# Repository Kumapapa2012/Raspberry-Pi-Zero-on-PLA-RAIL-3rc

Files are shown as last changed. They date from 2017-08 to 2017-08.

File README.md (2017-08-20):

# ※注意: 使用 Raspbian について
こちらの内容は、Raspbian の最新イメージ(2017-08-16-raspbian-stretch-lite.img)では動作しません(uv4l がインストールできません)。
これまで Debian8 ベースであったものが、最新版から、Debian9 ベースに変更されたためです。
試す場合はお手数ですが、こちらから、7/15 バージョンもしくはそれ以前を入手して使用してください。

Lite 版
http://downloads.raspberrypi.org/raspbian_lite/images/

通常 版
http://downloads.raspberrypi.org/raspbian_lite/images/

# Raspberry-Pi-Zero W 搭載プラレールについて
去年、Raspberry-Pi Zero の発売と同時に[初代プラレール](https://github.com/Kumapapa2012/Raspberry-Pi-Zero-on-PLA-RAIL)を作成。
これは USB の　Web カメラ、Wifi Dongle などをつけるため、 USB ハブを接続していました。  

しかし今年、Raspberry-Pi Zero W を運よく入手でき、これをプラレールに搭載しました。  
Wifi-Dongle が不要になり、またRaspberry-pi Camera モジュールを使用することで、USB WebCam も不要になりました。  
さらに最近は Zero-LiPo という Lipo バッテリーをRaspberry Pi Zero で使用するためのパーツも販売されており、これも使用しました。  
その結果、かなりすっきりとした構造になりました。  
ここでは、作成方法と、動かすためのコードを公開します。  


# 材料
## プラレール S-61　E233系湘南色 (単二電池バージョン)
<http://www.takaratomy.co.jp/products/lineup/detail/plarail470663.html>  
単二電池バージョンのE233系です。  
最近のプラレールは単三電池バージョンが主流ですが、単二電池バージョンもまだ上記タカラトミーの公式サイトで販売しています。  
アマゾンなどでも購入可能と思われます。

## Raspberry Pi Zero W
<https://www.switch-science.com/catalog/3200/>  
技適の関係で、日本取り扱い店からの入手が必要ですが、2017/08 現在入手しづらい状況が続いています。

## Raspberry Pi Camera Module + Cable
<https://shop.pimoroni.com/products/raspberry-pi-camera-module-v2-1-with-mount>  
<https://shop.pimoroni.com/products/camera-cable-raspberry-pi-zero-edition>  
Raspberry Pi Zero に取り付けるカメラとケーブル。  
Zero のカメラコネクタは通常の Raspberry Pi とサイズが全く異なるため、専用ケーブルが必要です。  
最近、Zero 専用のカメラも出ましたので、こちらを使用するのもいいかもしれません。  
<https://shop.pimoroni.com/products/raspberry-pi-zero-camera-module>

## Zero Lipo
<https://www.switch-science.com/catalog/3216/>
Li-PoバッテリーをRaspberry Pi シリーズで使用できるようにする電源コンバーターです。  
なお、今回はバッテリーコネクタを切除し、カメラと干渉する部分を切断しています。
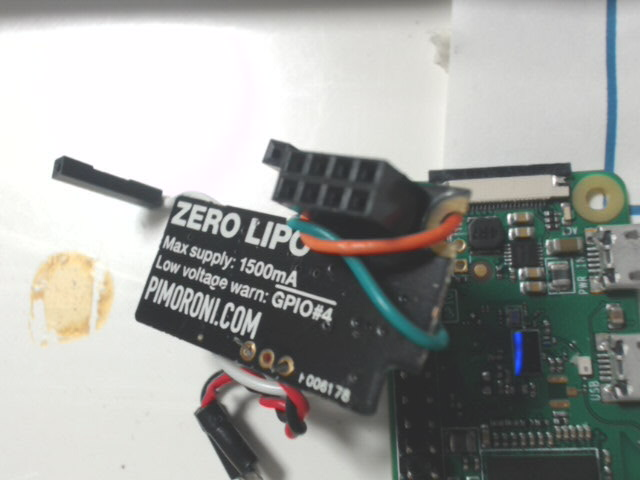
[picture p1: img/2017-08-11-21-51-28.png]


## Li-Po　バッテリー
<https://www.amazon.co.jp/gp/product/B01KC2JVB4/ref=oh_aui_detailpage_o04_s00?ie=UTF8&psc=1>  
Amazon で購入した、5個パック+充電器のセット。かなりコスパが良い。

## 電子部品
秋月電子さんや千石電商さんで購入。また、抵抗などは自宅にある適当なものを使用しています。  
以下の表にまとめます。

|種別|名称|備考|
|:-|:-|:-|
|モーターコントローラー|TA7291P|PWM によるモーター制御を行う|
|抵抗|R1|10kΩ - TA7291P の Vref-Vs間で、回路保護のため。|
|抵抗|R2|3.0Ω - Vs への入力電流の制限用|
|抵抗|R3|１kΩ - ヘッドランプ LED 用|
|LED|LED1,LED2|白色 LED ヘッドランプ用。|
|電解コンデンサ|C1|10V2200μF - 電圧降下の抑制用パスコン|
|コネクタ・ケーブル類|-|手持ちのものを使用|

## その他部品
バランス調整のため板おもりも使用しました。  
<https://www.amazon.co.jp/%E7%AC%AC%E4%B8%80%E7%B2%BE%E5%B7%A5-22170-%E6%9D%BF%E3%82%AA%E3%83%A2%E3%83%AA4m%E5%B7%BB%E3%82%AD-0-25mm/dp/B000AR6W00>

# 構造
モーター部とバッテリー部の2両で構成されています。
目測と手合わせだけで位置を決め、カッターやルーターでガリガリ切削して作っていますので図面等は存在しません。
このため、すべて写真で説明します。
※なお、以降の写真ではヘッドライトの LED が 1 つしかありません。これは先日結線が切れてしまい、外したためです。しかし以下の説明は、LED を2つ使うものとして記述します。

## 1 両目
Raspberry Pi Zero W とカメラ、モータードライバを搭載しています。カメラ画像は Motion JPEG ストリーミングしています。モータードライバでモーターの回転を制御します。  
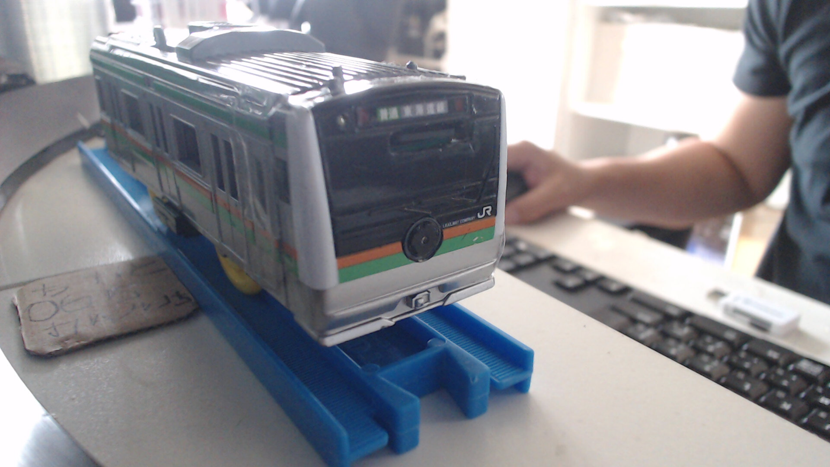
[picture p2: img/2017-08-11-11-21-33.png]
  
シャーシとの分離。  
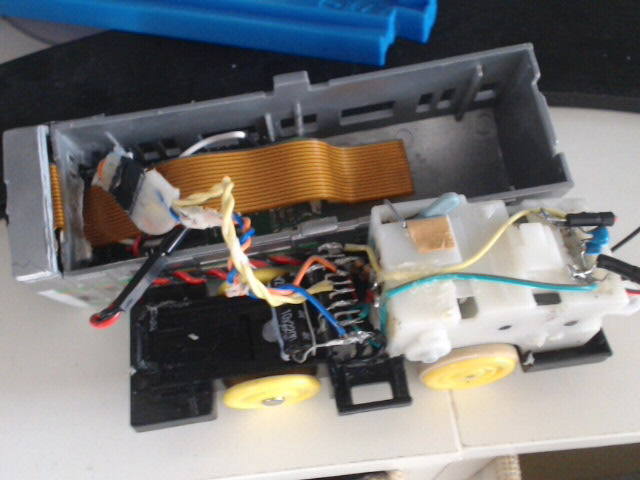
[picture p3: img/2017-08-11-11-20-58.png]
  
ケーブルを外したところ。  
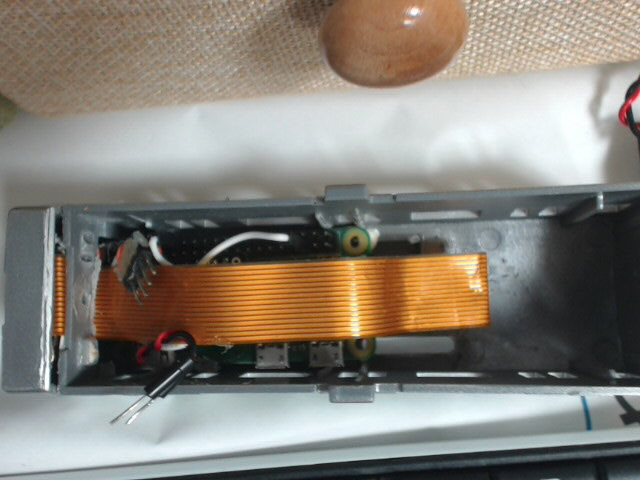
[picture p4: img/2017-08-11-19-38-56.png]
  
カメラケーブルを外したところ。  
中心の右下横のスイッチ穴に干渉しないよう、 Raspberry Pi Zero をはめています。こうしないと、ギヤボックスとRaspberry Pi Zero が干渉し、ボディがシャーシに嵌まりません。  
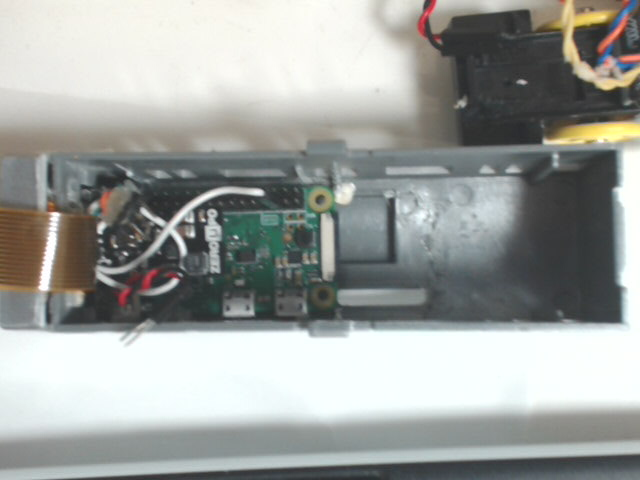
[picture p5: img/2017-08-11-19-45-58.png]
  
SD カードの突起により、スイッチ穴との干渉が発生したため、穴を開けて対処しています。  
結果的に、すぐに SD カードを取り出せるようになっています。  
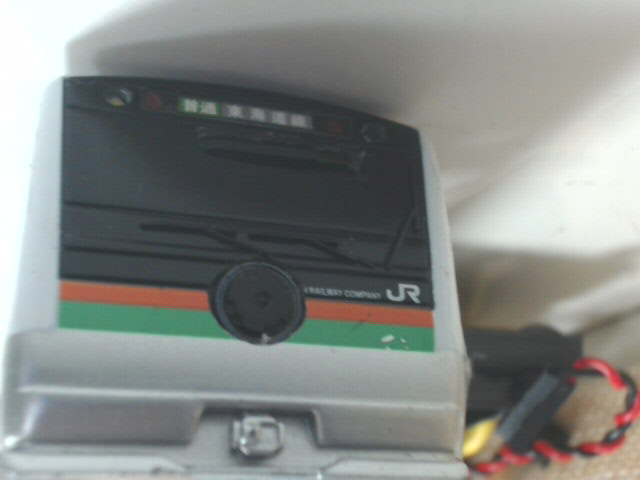
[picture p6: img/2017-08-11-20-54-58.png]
  
カメラの格納。運転席部分にすっぽりと収まります。  
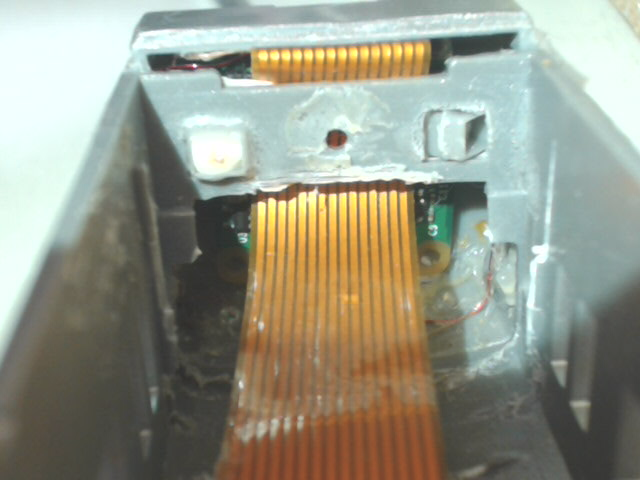
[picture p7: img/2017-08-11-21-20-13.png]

上から見たところ。ケーブルを下部にすることで、ケーブルが Raspberry Pi Zero と干渉するのを避けています。  
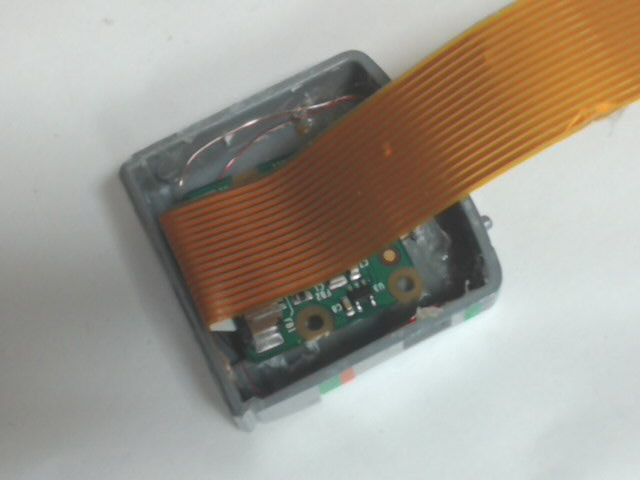
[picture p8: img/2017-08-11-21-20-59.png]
  
レンズの穴の位置も、やはり手合わせで決めています。  
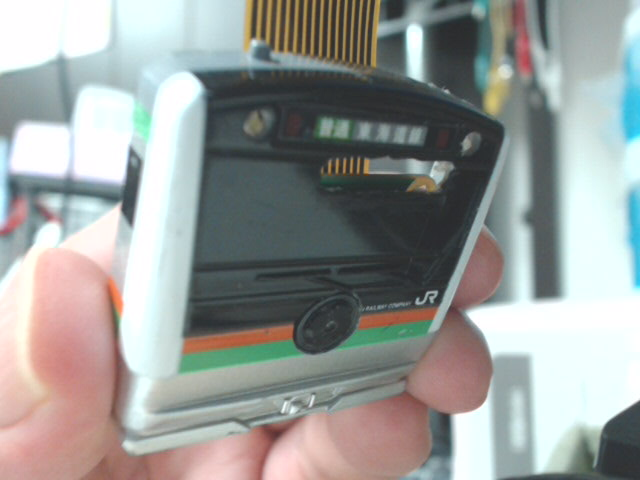
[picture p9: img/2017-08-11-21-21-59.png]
  
ボディ前方を大幅に切削したため運転席部分は保持できず、テープで止めています。  
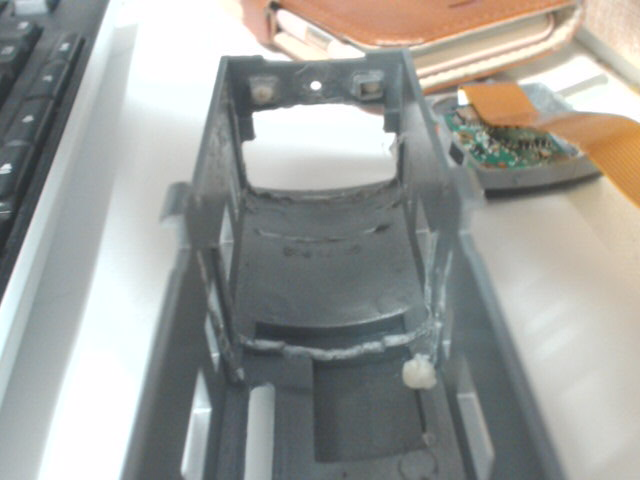
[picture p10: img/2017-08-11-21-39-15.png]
  
シャーシです。ハンダ付けが非常に雑で恥ずかしいのですが、一応問題なく機能しています。  
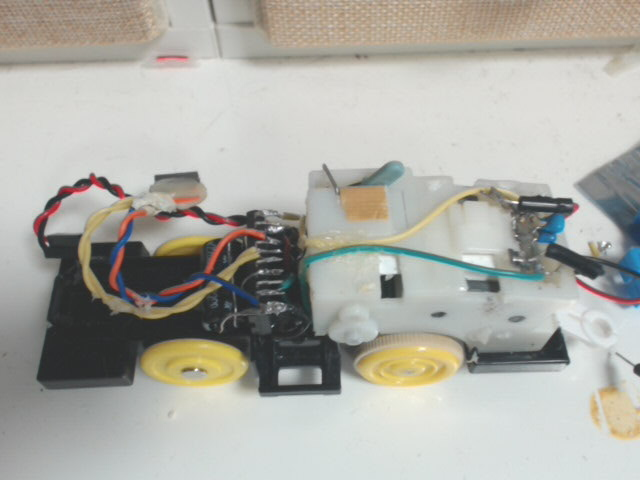
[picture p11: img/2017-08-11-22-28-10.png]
  
モータードライバとパスコンです。ハンダ付けが非常に汚く、見苦しいと思いますがご容赦ください。  
配線の詳細は別途記載する配線図にてご確認ください。  
なおパスコンは動作の安定化のためつけています。容量は適当です。  
これがないと、発進時にカーネルパニックを起こしがちです。  
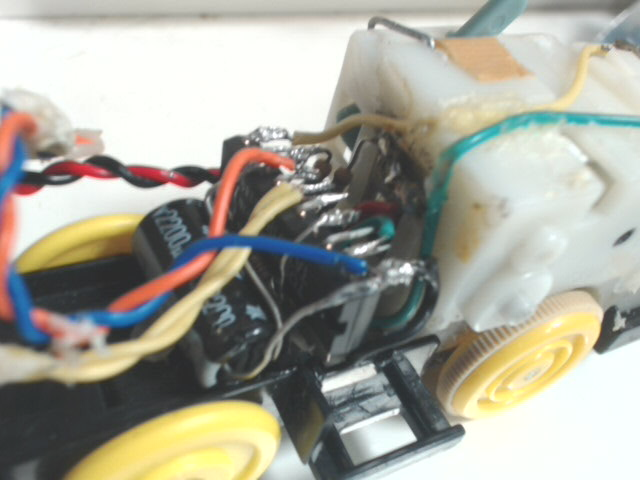
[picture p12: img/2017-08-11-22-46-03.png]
  
ギアボックスは 2 段階変速ですが、 1 段目のみ使用するようにストッパーを設けています。これはモータ負荷による起電力低下の緩和のためですが、そもそもブラウザでモーターの無段階変速を行いますので、ギアによる変速は無用です。  
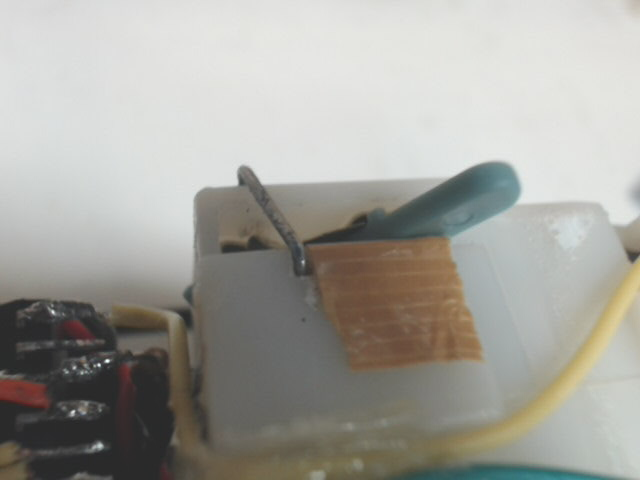
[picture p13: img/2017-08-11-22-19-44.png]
  
単二電池仕様のプラレールですので、電池がない状態では前輪が浮くことがあります。  
それを防止するため、前方下部におもりをつけています。板おもりを丸めて作成しています。
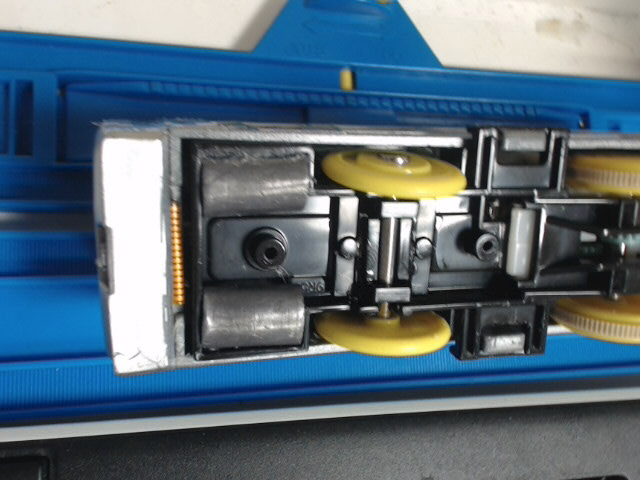
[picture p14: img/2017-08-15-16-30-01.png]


## 2 両目
Li-Po バッテリーを搭載しています。特に改造していません。 
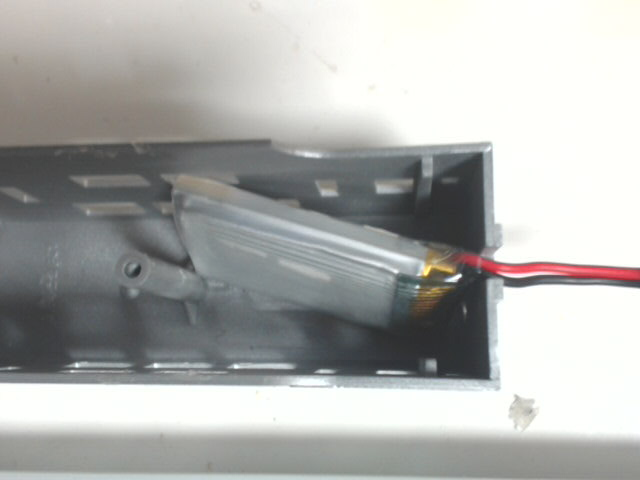
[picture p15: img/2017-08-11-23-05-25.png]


電池の充電は、車両ごと充電器に繋いで行います。
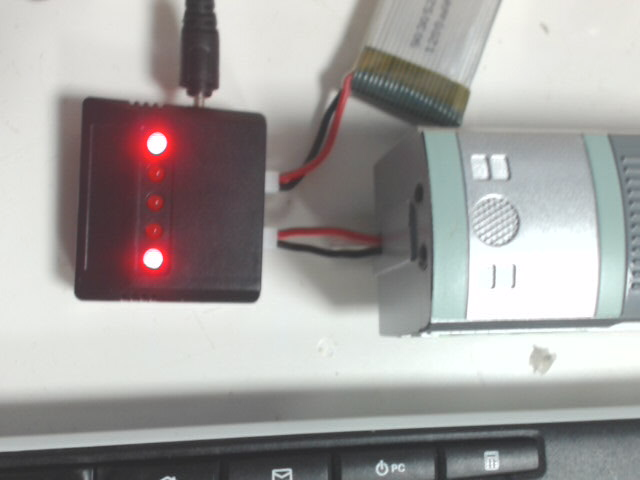
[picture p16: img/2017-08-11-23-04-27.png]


# ブレッドボード図/配線図
Fritzing で作成したブレッドボード図です。[Fritzing でも公開](http://fritzing.org/projects/raspberry-pi-zero-w-motor-control-with-zero-lipo-2)しています。   
左側ブレッドボードと Raspi の間の黒いチップは Zero LiPo です。  
なお図面では Raspberry Pi カメラモジュールは省略しています。  
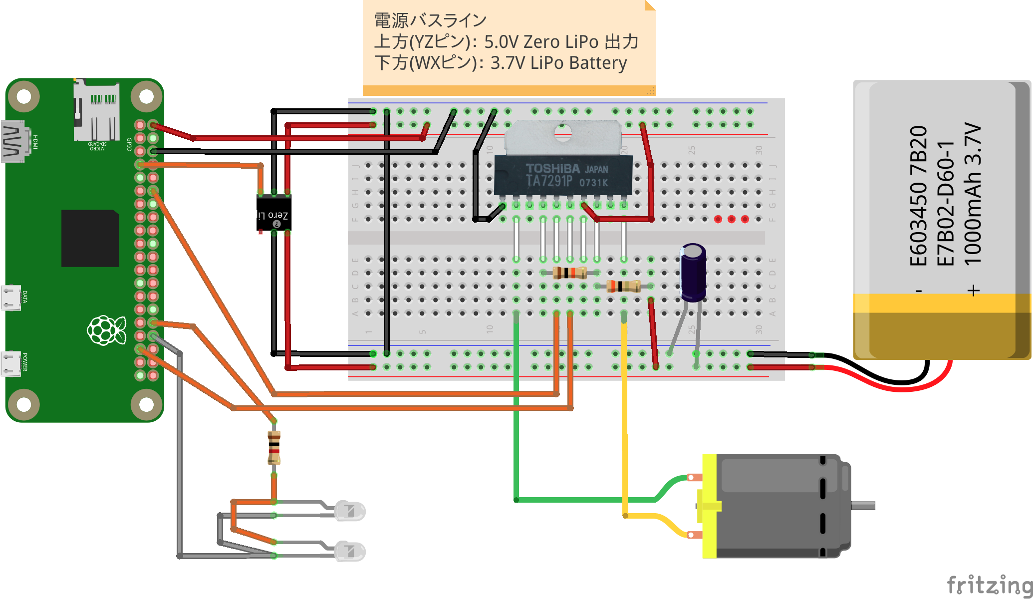
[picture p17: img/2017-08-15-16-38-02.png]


# ソフトウェア
プラレールは以下のような構成で動作します。
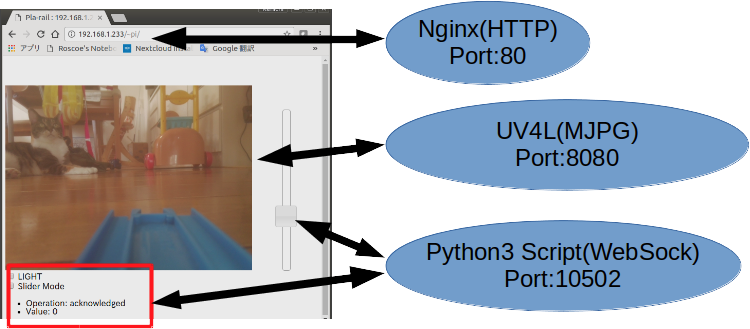
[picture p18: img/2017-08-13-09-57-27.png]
  
以下、セットアップ手順を説明します。  

## OS
SD カードにソフトウェアをインストールします。
OS は Raspbian 8 (Jessie) です。[公式サイト](https://www.raspberrypi.org/downloads/raspbian/)から入手してインストールしてください。  
OS のインストール後、"raspi-config" にて以下を有効化しておいてください。  
- Wifi 
- SSH 
- GPIO
- カメラ

また、Wifi経由の インターネットアクセス設定を行い、SSH で接続できることを確認しておいてください。  
これらの設定についてはここでは説明しません。

## Git からのファイル入手
本リポジトリにプラレール制御用ファイル群を公開しています。
SSH で Raspberry Pi Zero にログオンし、以下にて、Raspberry Pi Zero W にファイルを落としておきます。

$ cd ~  
$ sudo apt install git    
$ cd git  
$ git clone (本リポジトリのURL)  

## Nginx
ブラウザ等でプラレールをコントロールするページを表示するための Web サーバーになります。
### インストールと設定
apt でインストールします  

    $ sudo apt install nginx  

インストール後、``/etc/nginx/sites-available/default`` の ``"server {...}"``　セクションで、ユーザーフォルダの設定を行います。  
これにより、"http://hostname/~username/"で HTML コンテンツを公開できるようにします。  
以下を、``"server {...}"``　セクション内に追記します。

    location ~ ^/~(.+?)(/.*)?$ {  
        alias /home/$1/public_html$2;  
        index  index.html index.htm;  
        autoindex on;  
    }  

設定後、以下の作業を行い、ファイルを配置します。  

    $ cd ~  
    $ cp -R git/Raspberry-Pi-Zero-on-PLA-RAIL-3rd/public_html/ .

## UV4L
Motion JPEG による動画配信を行います。 "MJPEG Streamer" よりも新しく、取り扱いが簡単です。  
### インストールと設定
以下の手順でインストールします。  

    $ curl http://www.linux-projects.org/listing/uv4l_repo/lrkey.asc | sudo apt-key add -  
    $ sudo -s  
    # echo "deb http://www.linux-projects.org/listing/uv4l_repo/raspbian/ jessie main" >> /etc/apt/sources.list  
    # apt update  
    # apt install uv4l-webrtc uv4l-raspicam-extras  
    # exit  

インストール後、uv4l サービスを停止します。  

    $ sudo service uv4l_raspicam stop  

停止後、画像サイズを設定するため、"/etc/uv4l/uv4l-raspicam.conf" ファイルの以下のオプションを書き換えます。  

    width = 480  
    height = 360  
    framerate = 15  

書き換え後、uv4l サービスを起動します。  

    $ sudo service uv4l_raspicam start

## Python3 Script
モーター及び LED の制御を行います。  
WebSocket サーバーとして動作し、ブラウザ上で双方向リアルタイム制御を行うための機能を実装しています。  
### インストールと設定
以下インストールします。

    $ sudo apt install python3 python3-rpi.gpio python-pip python3-pip  
    $ pip3 install asyncio websockets

インストール後、以下のようにファイルを配置します。  

    $ cd ~  
    $ sudo cp -R git/Raspberry-Pi-Zero-on-PLA-RAIL-3rd/bin/ /opt/pla-rail/

起動時にスクリプトが動作するように、以下の作業を行います。

    $ sudo -s
    # crontab -e
    **** 表示された内容の最後に以下を記し保存します。****  

    # Run wsock_svr.py at boot time
    @reboot python3 /opt/pla-rail/wsock_svr.py &  

    **** 保存後 Root 状態から出ます。****  
    # exit  
    $

# テスト
一度 OS を再起動し、しばらくしてからブラウザで "http://(IP Address)/~pi/" を開きます。
以下のように画面が開き、カメラの映像が見えれば、起動しています。  
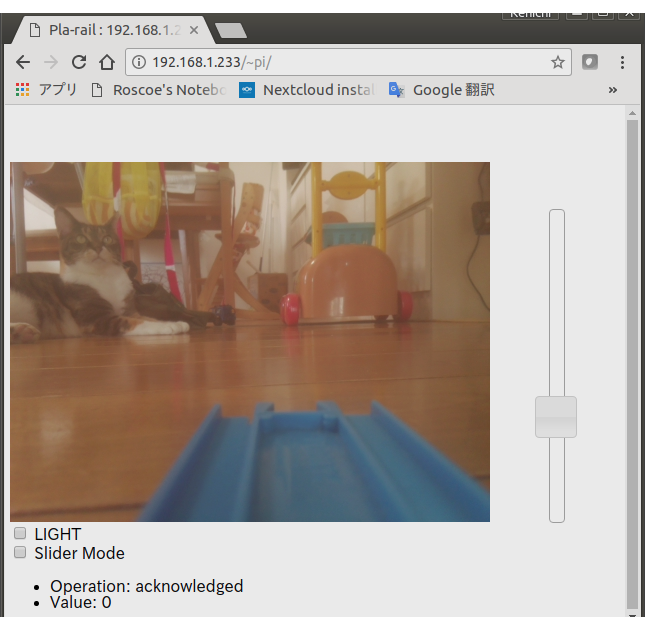
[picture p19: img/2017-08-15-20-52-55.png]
   
なお、"Operation..." が表示されていない場合、Python3 の WebSocket サーバーが動作していません。  
スクリプトが起動失敗していないか確認してください。

# 注意点
今回の場合、Zero Ripo バッテリー容量低下シグナル(GPIO4)の読み取りと通知は使用できません。これは、 1 つの LiPo バッテリーをモーター駆動と Raspberry Pi Zero 駆動の両方に使用しているためです。  
Zero Ripo バッテリー容量低下シグナルは起電力が 3.4V 程度になった場合に稼働しますが、今回の回路では、 3.8V 程度ですでに電力不足となり、モーター駆動の瞬間にダウンするようになります。このため、バッテリーの起電力が 3.4V 程度になるまで使用することはありません。

# 参考とさせていただいた文書
[Raspberry Pi 3 の標準カメラで撮影した動画をブラウザに配信する方法まとめ](http://qiita.com/okaxaki/items/72226a0b0f5fab0ec9e9#%E9%85%8D%E4%BF%A1%E6%96%B9%E6%B3%952---uv4l-raspicam)  
[Pythonスクリプトをサービスで起動させる](http://qiita.com/okhiroyuki/items/d19e8b0c4599767955a8)

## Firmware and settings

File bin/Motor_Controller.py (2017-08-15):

#!/usr/bin/env python3
# -*- coding: utf-8 -*-

import RPi.GPIO as GPIO
import time


class Motor_Controller:
	def __init__(self):
		# 初期化、BCM18→PWM0、BCM19→PWM1
		pwm0_pin=18
		pwm1_pin=19

		GPIO.setmode(GPIO.BCM)
		GPIO.setup(pwm0_pin, GPIO.OUT) 
		GPIO.setup(pwm1_pin, GPIO.OUT)
		
		self.pwm0=GPIO.PWM(pwm0_pin, 50)
		self.pwm1=GPIO.PWM(pwm1_pin, 50)

		self.pwm0.start(0)
		self.pwm1.start(0)


	def motor_run(self, duty):
		if duty>100: duty=100
		elif duty<-100: duty=-100
		absduty = min(abs(duty),100)
		
		if duty>0:
			self.pwm0.ChangeDutyCycle(absduty)
			self.pwm1.ChangeDutyCycle(0)
		elif duty<0:
			duty = max(abs(duty),100)
			self.pwm0.ChangeDutyCycle(0)
			self.pwm1.ChangeDutyCycle(absduty)
		else: # duty==0
			self.pwm0.ChangeDutyCycle(0)
			self.pwm1.ChangeDutyCycle(0)

	def __del__(self):
		GPIO.cleanup()

if __name__ == "__main__":
	pass

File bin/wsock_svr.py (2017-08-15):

#!/usr/bin/python3
# -*- coding: utf-8 -*-
import asyncio
import websockets
import json
# motor controller
import Motor_Controller

# light:
import RPi.GPIO as pin_bcm12
pin_bcm12.setmode(pin_bcm12.BCM)
pin_bcm12.setup(12, pin_bcm12.OUT) 

# Todo: ここらでモーターコントローラー初期化
mc = Motor_Controller.Motor_Controller()

# Todo: Duty 比の値を保持する整数初期化（-100 to 100）
duty = 0

# Light Flag
flg_light = False

connected = set()

def process_msg(data):
	global flg_light
	global duty

	str_type = data["type"]
	if str_type == "change":
		duty = data["value"]
		# ここでモーターコントローラーに値セット
		# 単純に、値を PWM のデューティ比に設定すればいい。
		# mc.motor_run(int(duty))
		# ※今回、配線の結果、duty は 負値で前進となってしまった。
		mc.motor_run(int(duty) * -1)
            
	elif str_type == "light":
		light_flg = data["value"]
		# ==0:Off / !=0:On
		if(light_flg == 0):
			# GPIO 12(BCM)
			pin_bcm12.output(12, 0)
			flg_light = False
		else:
			pin_bcm12.output(12, 1) 
			flg_light = True

	elif str_type == "mode":
		print("str_type: mode : Do Nothing.")
	else:
		# do nothing
		print("unknown str_type:"+str_type)

@asyncio.coroutine
def controll_handler(websocket, path):
    global connected
    global duty
    global flg_light
    # Register
    connected.add(websocket)
    js_msg = {'type':'accepted',
    	'remote_address':websocket.remote_address}
    yield from websocket.send(json.dumps(js_msg))
    # 暫定:個別に初期値を送信。
    # 今後初期値のクライアントへの送信方法は変更すべき。
    js_msg = {'type':'change',
    	'value':duty}
    yield from websocket.send(json.dumps(js_msg))

    js_msg = {'type':'light',
    	'value':int(flg_light)}
    yield from websocket.send(json.dumps(js_msg))
    


    try:
        # Send current value: JSON.
        # msg = '{"type":"change","value":'+str(duty)+'}'
        while 1:
            msg = yield from websocket.recv()
            # JSON 形式の値を読み取り
            print(msg)
            data = json.loads(msg)
			# データに応じた処理
            process_msg(data)

            # クライアントに送信
            for ws in connected:
            	if (websocket.remote_address == ws.remote_address): 
            		#送信者のコマンドの場合は Type を上書きする。
            		str_type = 'acknowledged'
            	else:
            		str_type = data['type']
            	js_msg = {'type':str_type,
                	'value':str(data['value'])
                	}
            	yield from ws.send(json.dumps(js_msg))

    except:
        print('!!!!')	
        connected.remove(websocket)
    
start_server = websockets.serve(controll_handler, '0.0.0.0', 10502)

asyncio.get_event_loop().run_until_complete(start_server)
asyncio.get_event_loop().run_forever()

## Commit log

2017-08-15 Upload All
    [Circuit-BreadBoard.fzz]
2017-08-20 Raspbian について注意追記
    Raspbian について注意追記
